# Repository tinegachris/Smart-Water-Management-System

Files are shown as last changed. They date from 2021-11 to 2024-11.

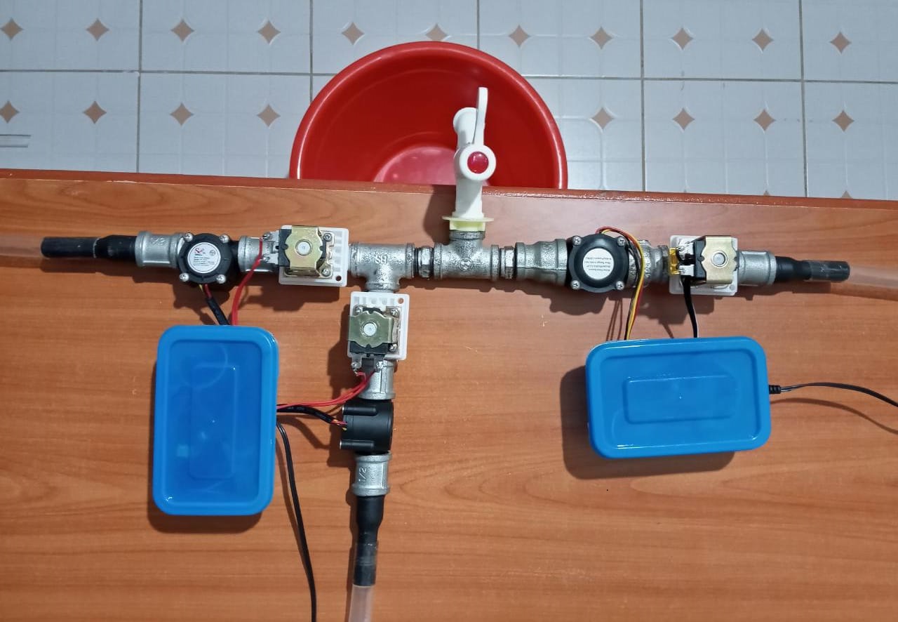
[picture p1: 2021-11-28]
system pic.jpeg

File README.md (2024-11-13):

# Smart-Water-Management-System

>Final Project 2021











system pic

## Abstract

The Smart Water Management System project aggregates three meters to enable remote and automatic real-time measurement of water consumption. Based on actionable decisions such as water leakage and consumption metrics, water supply through the pipes is controlled using solenoid valves. The consumer and the supplier can monitor, visualize consumption metrics and control the system through the designed android interface.

## Acknowledgement

I acknowledge the efforts of my project partner Mr [Thoenes Kimani](https://www.linkedin.com/in/thoenes-kimani-607682186/) and my project supervisor Mr [Samson N. Njoroge](https://www.linkedin.com/in/samson-n-njoroge-23a77817/?originalSubdomain=ke), for ensuring this project was successful. Many thanks to all our friends and family for the encouragement and support throughout the period.

## System Overview

The system consists of four functional modules, namely: the physical device, the gateway through which the device communicates with the backend service, the backend that allows storage of data, analysis, data access and notifications and the interface that allows visualization and control.

>

## Concept Diagram

The Concept Diagram provides an overview of the system's architecture, illustrating the main components and their relationships. It helps in understanding the high-level design and the flow of data between different parts of the system.

The system consists of three meters: the supply meter, 1 and customer meters, 2 and 3 as shown below.

>

You can view and edit the detailed Concept Diagram using the provided `.vsdx` file using Microsoft Visio app:

- [Concept Diagram.vsdx](https://github.com/tinegachris/Smart-Water-Management-System/blob/e62496e4574b8286091f124c95a754fc847280cd/Concept%20Diagram.vsdx)

## System Flow Chart

The System Flow Chart illustrates the step-by-step flow of operations within the Smart Water Management System. It shows the sequence of actions and decision points, making it easier to understand the system's logic and workflow.

>

You can view and edit the detailed System Flow Chart using the provided `.vsdx` file using Microsoft Visio app:

- [System Flow Chart.vsdx](https://github.com/tinegachris/Smart-Water-Management-System/blob/e62496e4574b8286091f124c95a754fc847280cd/System%20flow%20chart.vsdx)

## System Components

1. **Three NodeMCU ESP8266** - [Component Overview](https://components101.com/development-boards/nodemcu-esp8266-pinout-features-and-datasheet)
2. **Three YF-S201 Hall Effect Water Flow Sensor** - [Component Overview](https://components101.com/sensors/yf-s201-water-flow-measurement-sensor)
3. **Three 2 Way, 2 Position, 12 VDC, 0.5 Inch, NC Solenoid Valve** - [Particular](https://www.twinschip.com/Solenoid_Valve_DC12V_0.5inch_Normally_Closed) ~~Not an affiliate link~~
4. **Three SRD-05VDC-SL-C Relay Module** - [Component Overview](https://elearn.ellak.gr/mod/book/view.php?id=4568&chapterid=2440)
5. **Three Power Supply Adapter 12V 2A**
6. **0.5 Inch Clear hose pipe - approx. 3 meters**
7. **One 0.5 Inch Plastic tap**
8. **Appropriate pipe fittings**

## Schematic Diagram

The schematic diagram of the system was designed using Autodesk's Eagle EDA software illustrating how the various components are interconnected.

Custom libraries for the solenoid valve and the water flow sensor were created.

>sch

## PCB Design

Design of the board from the schematic diagram was done as shown below.

>brd

## Firmware Walkthrough

- **Libraries**

The ESP8266WiFi, ESP8266WebServer, ESP8266mDNS and the ThingSpeak libraries were included.

```
#include <ESP8266WiFi.h> // ESP8266WiFi library
#include<ESP8266WebServer.h> // WebServer library
#include <ESP8266mDNS.h> // mDNS library
#include<ThingSpeak.h> // ThingSpeak library
```

- **Variables and Constants**

The variables and constants were defined as follows.

```
const int measuringInterval = 0.1 * 1000; // measure flow every 1 second
const int postingInterval = 15 * 1000; // post data every 15 seconds

long currentMillis = 0, previousMillis = 0;

float calibrationFactor_1 = 0.1;
volatile byte pulseCount_1;
byte pulse1Sec_1 = 0;
float flowRate_1;
unsigned long flowMilliLitres_1, totalMilliLitres_1;
float flowLitres_1, totalLitres_1;

// Control solenoid valve
const int controlChannelID = XXXXXXX; //ThingSpeak channel used for control
unsigned int valve1 = 4;
```

- **Wi-Fi Settings**

The SSID and password are set to allow the NodeMCU to connect to a network

```
const char* ssid = "mySSID"; // wireless network name (SSID)
const char* password = "myPassword"; // Wi-Fi network password
```

- **ThingSpeak Settings**

ThingSpeak credentials and API key are set to allow sending data to specific channel.

```
// ThingSpeak Settings
const int channelID = YYYYYYY;
String writeAPIKey = "XXXXXXXXXXXXXXXX";
const char* server = "api.thingspeak.com";
```

- **Serial Communication**

The baud rate for serial communication  set was to 115200.

```
  void setup() {
  Serial.begin(115200); // Start the Serial communication
  delay(100);
```

- **Define pins and initialize variables**

```
  pulseCount_1 = 0;
  flowRate_1 = 0.0;
  flowMilliLitres_1 = 0;
  totalMilliLitres_1 = 0;
  
  pinMode(flowSensor_1, INPUT_PULLUP);  
  pinMode(relayValve_1, OUTPUT);
  digitalWrite(relayValve_1, 0);
```

- **Connect to Wi-Fi network**

The NodeMCU waits until it is connected to a network then sends the IP address, Netmask and Gateway to the serial monitor.

```
WiFi.begin(ssid, password);             // Connect to the WiFi network
  Serial.print("Connecting to ");
  Serial.print(ssid); Serial.println("...");

  while (WiFi.status() != WL_CONNECTED) { // Wait for the Wi-Fi to connect
    delay(500);
  }
  
  Serial.println("WiFi connected!"); 
  // Send the IP address of the ESP8266 to serial monitor 
  Serial.print("IP address:\t");
  Serial.println(WiFi.localIP()); 
  // Send the Netmask of the ESP8266        
  Serial.print("Netmask:\t");
  Serial.println(WiFi.subnetMask());  
  // Send the Gateway of the ESP8266
  Serial.print("Gateway:\t");
  Serial.println(WiFi.gatewayIP());
```

- **Measure Wi-Fi Strength**

The Wi-Fi strength is measured and sent to the serial monitor.

```
// Measure Signal Strength (RSSI) of Wi-Fi connection
long rssi = WiFi.RSSI();
String strgth = String(rssi);
Serial.println("signal strength: " + strgth + "dB\n");
```

- **HTTP server**

The HTTP server that listens for HTTP request on port 80. The mDNS responder is also started to resolve IP address to a local domain name.

```
  // Create a webserver object that listens for HTTP request on port 80
  ESP8266WebServer server(80);

  // Start the mDNS responder for esp8266.local
  if (MDNS.begin("esp8266")) {              
  Serial.println("mDNS responder started");
  } else {
    Serial.println("Error setting up MDNS responder!");
  }

  server.begin(); // Actually start the server
  Serial.println("HTTP server started");
  
  //create interrupt and call a function when change is detected
  attachInterrupt(digitalPinToInterrupt(flowSensor_1), pulseCounter_1, FALLING);

  ThingSpeak.begin(client);
```

- **FLow Sensor Interrrupt**

An interrupt and a call function is created to detect water flow when the falling edge of the pulse is received.

```
//create interrupt and call a function when change is detected
  attachInterrupt(digitalPinToInterrupt(flowSensor_1), pulseCounter_1, FALLING);
```

The pulse count is incremented for every pulse that is detected.

```
void IRAM_ATTR pulseCounter_1(){
  pulseCount_1++;
}
```

- **Flowrate and Volume Calculation**

The flowrate and volume through the meter is measured and calculated after every measuring interval. The total volume is the cumulative volume in the entire measuring time.

```
currentMillis = millis();
  // calculate after every measuring interval
  if (currentMillis - previousMillis > measuringInterval) {
    
    pulse1Sec_1 = pulseCount_1;
    pulseCount_1 = 0;

     //calculate flow rate in litres per min
    flowRate_1 = ((1000.0 / (millis() - previousMillis)) * pulse1Sec_1) / calibrationFactor_1;
    previousMillis = millis();

    //flowrate in millilitres per second
    flowMilliLitres_1 = (flowRate_1 / 60) * 1000;

    //flowrate in litres per second
    flowLitres_1 = (flowRate_1 / 60);

    //add volume flowed in this second to cumulative totals
    totalMilliLitres_1 += flowMilliLitres_1;
    totalLitres_1 += flowLitres_1;

    // Print the flow rate 1 for this second in litres / minute
    Serial.print("Flow rate 1: ");
    Serial.print(flowMilliLitres_1);
    Serial.print(" mL/s\t");
    
    // Print the cumulative total of litres flowed through meter 1 since starting
    Serial.print("Volume through meter 1: ");
    Serial.print(totalMilliLitres_1);
    Serial.print(" mL\n");
//    Serial.println("Volume through meter 1: "); //Uncomment for volume in litres
//    Serial.print(totalLitres_1);
//    Serial.println(" L\n");
```

- **API request body**

The body of API request with consumption data are constructed waiting to be posted to ThingSpeak on specific fields.

```
      // Construct API request body
      String body = "field1=";
      body += String(float(flowRate_1));
      body += "&field2=";
      body += String(totalMilliLitres_1);
      body += "&field3=";
      body += strgth;
      body += "\r\n\r\n";
```

- **Post to ThingSpeak**

The API requests bodies are written to the corresponding fields on ThingSpeak on the specified channel. Feedback on if the data was sent successfully is sent to the serial monitor.

```
      client.print("POST /update HTTP/1.1\n");
      client.print("Host: api.thingspeak.com\n");
      client.print("Connection: close\n");
      client.print("X-THINGSPEAKAPIKEY: " + writeAPIKey + "\n");
      client.print("Content-Type: application/x-www-form-urlencoded\n");
      client.print("Content-Length: ");
      client.print(body.length());
      client.print("\n\n");
      client.print(body);
      client.print("\n\n");
      Serial.println("data sent\n");
```

- **Solenoid Valve Status**

The status of solenoid valve i.e. if it is open or closed is checked from the control feed and status sent to the serial monitor.

```
      //get the last data of the fields
      int valve_1 = ThingSpeak.readFloatField(controlChannelID, valve1);
    
      if(valve_1 == 1){
        digitalWrite(relayValve_1, 1); // Open solenoid valve
        Serial.println("Solenoid valve is Closed!\n");
        }
      else if(valve_1 == 0){
        digitalWrite(relayValve_1, 0); //Close solenoid valve
        Serial.println("Solenoid valve is Open!\n");
        }
```

- **Wait and Post Again**

```
    client.stop();
    
    Serial.print("Waiting ");
    Serial.print(postingInterval/1000);
    Serial.print(" seconds to post again...\n");
    
    // wait and then post again
    delay(postingInterval);
```

## **ThingSpeak Apps**

- ### MATLAB Analysis

The MATLAB Analysis app was used to perform loss analysis as shown below.

>

- ### ThingTweet

The ThingTweet app is utilized to send alert consumers via a tweet that the supply meter valve is closed due to any predetermined circumstance is encountered. The tweet is configured as below.

>

- ### TimeControl

TimeControl app feature was used in loss analysis calculation where losses due to leakages was calculated every 5 minutes as shown in the configuration below.

>

- ### React

React app feature was also used in the project in several instances such as sending email, SMS and VoIP calls when a certain condition is encountered.

>

## App Installation and Usage Instructions

### Installing the Smart Water App

#### For Developers (Using .aia File)

1. **Download the .aia File:**
   - Download the [Smart_Water_App.aia](https://github.com/tinegachris/Smart-Water-Management-System/blob/main/Smart_Water_App.aia) file from the repository.

2. **Open MIT App Inventor:**
   - Go to [MIT App Inventor](https://appinventor.mit.edu/).

3. **Import the .aia File:**
   - Click on "Projects" in the top menu.
   - Select "Import project (.aia) from my computer".
   - Choose the downloaded .aia file and click "OK".

4. **Build the App:**
   - After importing, you can modify the app as needed.
   - To build the app, click on "Build" in the top menu and select "App (provide QR code for .apk)" or "App (save .apk to my computer)".

#### For Users (Using .apk File)

1. **Download the .apk File:**
   - Download the [Smart_Water_App.apk](https://github.com/tinegachris/Smart-Water-Management-System/blob/main/Smart_Water_App.apk) file from the repository.

2. **Enable Unknown Sources:**
   - On your Android device, go to "Settings".
   - Navigate to "Security" or "Applications" (depending on your device).
   - Enable "Unknown sources" to allow installation of apps from sources other than the Google Play Store.

3. **Install the App:**
   - Open the downloaded .apk file on your Android device.
   - Follow the on-screen instructions to install the app.

### Using the Smart Water App

1. **Open the App:**
   - Locate the Smart Water App icon on your device and open it.

2. **Login:**
   - Enter your credentials to log in to the app.

3. **Monitor and Control:**
   - Use the app interface to monitor water consumption metrics.
   - Control the water supply through the solenoid valves remotely.

4. **Alerts and Notifications:**
   - Receive alerts and notifications for water leakage and other actionable events.

## **Interface**

The android app used as interface to visualize consumption data and control water supply remotely was designed using [MIT App Inventor](https://appinventor.mit.edu/).

The [.aia source code](https://github.com/tinegachris/Smart-Water-Management-System/blob/main/Smart_Water_App.aia) file is attached.

Download and install the [android app](https://github.com/tinegachris/Smart-Water-Management-System/blob/main/Smart_Water_App.app)

> login                   

## Results

The system utilized IoT solutions to enable remote and automatic and real-time measurement of water consumption data which is transmitted to a remote server for manipulation and analysis.

>

The data was then displayed on an interface where consumption metrics, over a period, was be viewed.

>                         

The system developed aggregated multiple meters and performed loss analysis hence detecting water leakage. SMS, call, email and [tweet](https://twitter.com/smart_water_app/status/1463631460607344641?t=qJkpamW6DDiH7IFD41dn9Q&s=19) alerts allowed appropriate actions to be taken.

> tweet               

Users could control water supply remotely from the interface based on actionable decisions.

> closed
> opened
> 

## Conclusion

The Smart Water Management System solution would be revolutionary for home and industrial systems by enabling remote and automatic measurement of consumption data, convenient monitoring and control of water systems and reducing water leakage - reducing non-revenue water hence saving on cost.

##

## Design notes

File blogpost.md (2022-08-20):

---
title: Smart Water Management System
domain: blog.chrispinetinega.com 
tags: Smart water system, Chrispine Tinega, IoT
subtitle: Final Project
/* The pathname of your article url 
* Ex. In https://engineering.hashnode.com/how-we-autodetect-spam-using-googles-vertex-ai 
"how-we-autodetect-spam-using-googles-vertex-ai" is the slug */ 
slug: smart-water-system
/* You need to upload your image to https://hashnode.com/uploader 
and use the uploaded image URL as COVER_IMAGE_URL */ 
cover: https://cdn.hashnode.com/res/hashnode/image/upload/v1660997561622/8FiyUe9cX.jpeg?auto=compress
/* When you have a team publication and a publication member has created an article */ 
/* Please note that this param is only supported while creating an article and not updating */ 
publishAs: Chrispine Tinega
/* When your article is republished and you want to use 
 the origin url as canonical url */ 
canonical: CANONICAL_URL_OF_ARTICLE 
/* Only if you don't want this article to be published yet */ 

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

>

## System Diagram
The system consists of three meters: the supply meter, 1 and customer meters, 2 and 3 as shown below.

>

## Flow Chart
The system’s flow chart diagram is as shown in the figure below.

>

## System Components

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

## Schematic Diagram

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

Custom libraries for the solenoid valve and the water flow sensor were created.

>sch

## PCB Design

Design of the board from the schematic diagram was done as shown below. 

>brd

## Firmware Walkthrough

- **Libraries**

The ESP8266WiFi, ESP8266WebServer, ESP8266mDNS and the ThingSpeak libraries were included.

```
#include <ESP8266WiFi.h> // ESP8266WiFi library
#include<ESP8266WebServer.h> // WebServer library
#include <ESP8266mDNS.h> // mDNS library
#include<ThingSpeak.h> // ThingSpeak library
```
- **Variables and Constants**

The variables and constants were defined as follows.
```
const int measuringInterval = 0.1 * 1000; // measure flow every 1 second
const int postingInterval = 15 * 1000; // post data every 15 seconds

long currentMillis = 0, previousMillis = 0;

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

// Control solenoid valve
const int controlChannelID = XXXXXXX; //ThingSpeak channel used for control
unsigned int valve1 = 4;
```

- **Wi-Fi Settings**

The SSID and password are set to allow the NodeMCU to connect to a network
```
const char* ssid = "mySSID"; // wireless network name (SSID)
const char* password = "myPassword"; // Wi-Fi network password
```

- **ThingSpeak Settings**

ThingSpeak credentials and API key are set to allow sending data to specific channel.
```
// ThingSpeak Settings
const int channelID = YYYYYYY;
String writeAPIKey = "XXXXXXXXXXXXXXXX";
const char* server = "api.thingspeak.com";
```

- **Serial Communication**

The baud rate for serial communication  set was to 115200.
```
  void setup() {
  Serial.begin(115200); // Start the Serial communication
  delay(100);
```

- **Define pins and initialize variables**

```
  pulseCount_1 = 0;
  flowRate_1 = 0.0;
  flowMilliLitres_1 = 0;
  totalMilliLitres_1 = 0;
  
  pinMode(flowSensor_1, INPUT_PULLUP);  
  pinMode(relayValve_1, OUTPUT);
  digitalWrite(relayValve_1, 0);
```

- **Connect to Wi-Fi network**

The NodeMCU waits until it is connected to a network then sends the IP address, Netmask and Gateway to the serial monitor.
```
WiFi.begin(ssid, password);             // Connect to the WiFi network
  Serial.print("Connecting to ");
  Serial.print(ssid); Serial.println("...");

  while (WiFi.status() != WL_CONNECTED) { // Wait for the Wi-Fi to connect
    delay(500);
  }
  
  Serial.println("WiFi connected!"); 
  // Send the IP address of the ESP8266 to serial monitor 
  Serial.print("IP address:\t");
  Serial.println(WiFi.localIP()); 
  // Send the Netmask of the ESP8266        
  Serial.print("Netmask:\t");
  Serial.println(WiFi.subnetMask());  
  // Send the Gateway of the ESP8266
  Serial.print("Gateway:\t");
  Serial.println(WiFi.gatewayIP());
```

- **Measure Wi-Fi Strength**

The Wi-Fi strength is measured and sent to the serial monitor.
```
// Measure Signal Strength (RSSI) of Wi-Fi connection
long rssi = WiFi.RSSI();
String strgth = String(rssi);
Serial.println("signal strength: " + strgth + "dB\n");
```

- **HTTP server**

The HTTP server that listens for HTTP request on port 80. The mDNS responder is also started to resolve IP address to a local domain name.
```
  // Create a webserver object that listens for HTTP request on port 80
  ESP8266WebServer server(80);

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

  ThingSpeak.begin(client);
```

- **FLow Sensor Interrrupt**

An interrupt and a call function is created to detect water flow when the falling edge of the pulse is received.
```
//create interrupt and call a function when change is detected
  attachInterrupt(digitalPinToInterrupt(flowSensor_1), pulseCounter_1, FALLING);
```
The pulse count is incremented for every pulse that is detected.
```
void IRAM_ATTR pulseCounter_1(){
  pulseCount_1++;
}
```

- **Flowrate and Volume Calculation**

The flowrate and volume through the meter is measured and calculated after every measuring interval. The total volume is the cumulative volume in the entire measuring time.
```
currentMillis = millis();
  // calculate after every measuring interval
  if (currentMillis - previousMillis > measuringInterval) {
    
    pulse1Sec_1 = pulseCount_1;
    pulseCount_1 = 0;

     //calculate flow rate in litres per min
    flowRate_1 = ((1000.0 / (millis() - previousMillis)) * pulse1Sec_1) / calibrationFactor_1;
    previousMillis = millis();

    //flowrate in millilitres per second
    flowMilliLitres_1 = (flowRate_1 / 60) * 1000;

    //flowrate in litres per second
    flowLitres_1 = (flowRate_1 / 60);

    //add volume flowed in this second to cumulative totals
    totalMilliLitres_1 += flowMilliLitres_1;
    totalLitres_1 += flowLitres_1;

    // Print the flow rate 1 for this second in litres / minute
    Serial.print("Flow rate 1: ");
    Serial.print(flowMilliLitres_1);
    Serial.print(" mL/s\t");
    
    // Print the cumulative total of litres flowed through meter 1 since starting
    Serial.print("Volume through meter 1: ");
    Serial.print(totalMilliLitres_1);
    Serial.print(" mL\n");
//    Serial.println("Volume through meter 1: "); //Uncomment for volume in litres
//    Serial.print(totalLitres_1);
//    Serial.println(" L\n");
```

- **API request body**

The body of API request with consumption data are constructed waiting to be posted to ThingSpeak on specific fields.
```
      // Construct API request body
      String body = "field1=";
      body += String(float(flowRate_1));
      body += "&field2=";
      body += String(totalMilliLitres_1);
      body += "&field3=";
      body += strgth;
      body += "\r\n\r\n";
```

- **Post to ThingSpeak**

The API requests bodies are written to the corresponding fields on ThingSpeak on the specified channel. Feedback on if the data was sent successfully is sent to the serial monitor.
```
      client.print("POST /update HTTP/1.1\n");
      client.print("Host: api.thingspeak.com\n");
      client.print("Connection: close\n");
      client.print("X-THINGSPEAKAPIKEY: " + writeAPIKey + "\n");
      client.print("Content-Type: application/x-www-form-urlencoded\n");
      client.print("Content-Length: ");
      client.print(body.length());
      client.print("\n\n");
      client.print(body);
      client.print("\n\n");
      Serial.println("data sent\n");
```

- **Solenoid Valve Status**

The status of solenoid valve i.e. if it is open or closed is checked from the control feed and status sent to the serial monitor.
```
      //get the last data of the fields
      int valve_1 = ThingSpeak.readFloatField(controlChannelID, valve1);
    
      if(valve_1 == 1){
        digitalWrite(relayValve_1, 1); // Open solenoid valve
        Serial.println("Solenoid valve is Closed!\n");
        }
      else if(valve_1 == 0){
        digitalWrite(relayValve_1, 0); //Close solenoid valve
        Serial.println("Solenoid valve is Open!\n");
        }
```

- **Wait and Post Again**

```
    client.stop();
    
    Serial.print("Waiting ");
    Serial.print(postingInterval/1000);
    Serial.print(" seconds to post again...\n");
    
    // wait and then post again
    delay(postingInterval);
```

## **ThingSpeak Apps**

- ### MATLAB Analysis 

The MATLAB Analysis app was used to perform loss analysis as shown below.

>

- ### ThingTweet

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

>

- ### TimeControl

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

>

- ### React

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

>

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

## Results

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

>

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

Users could control water supply remotely from the interface based on actionable decisions.

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

## Conclusion

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

##

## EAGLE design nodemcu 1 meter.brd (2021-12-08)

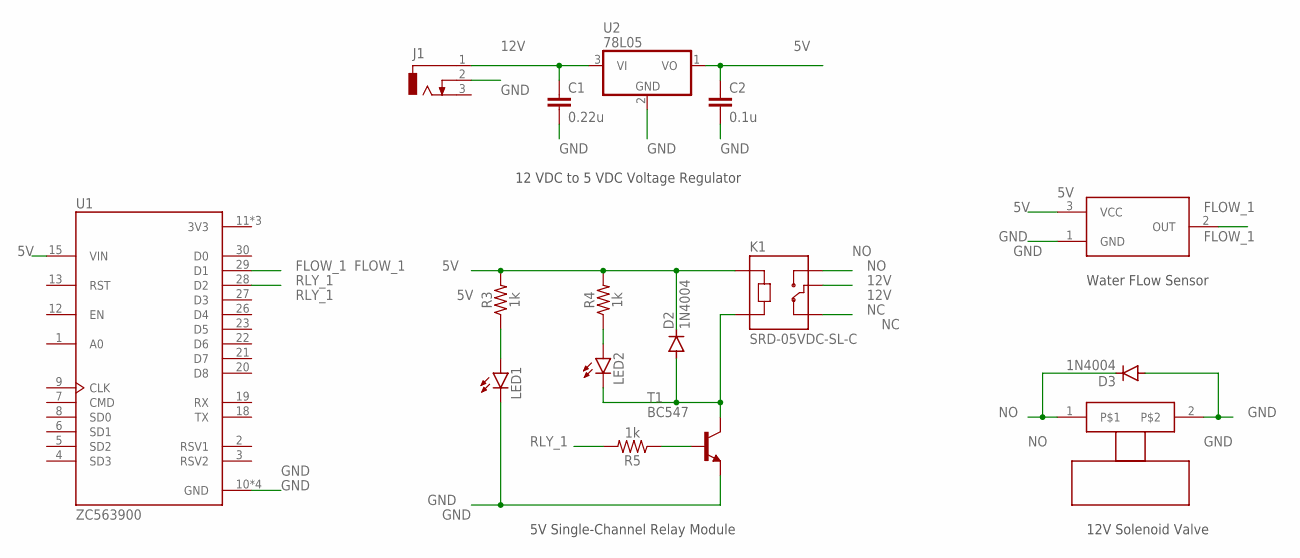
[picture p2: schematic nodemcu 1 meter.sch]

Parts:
C1: 0.22u; C025-025X050
C2: 0.1u; C025-025X050
D2, D3: 1N4004; DO41-10
FLOWSENSOR1: FLOWSENSOR
J1: DCJ0303
K1: SRD-05VDC-SL-C; RELAY_SRD-05VDC-SL-C
LED1, LED2: LED3MM
R3, R4, R5: 1k; AXIAL-0.3
T1: BC547; TO92
U1: ZC563900; MODULE_ZC563900
U2: 78L05; TO92
VALVE1: SOLENOID-VALVESOLENOID-CONNECTOR; 332-02

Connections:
3V3: U1.11 (3V3), U1.16 (3V3), U1.25 (3V3)
5V: C2.2, D2.C, FLOWSENSOR1.3 (VCC), K1.A1, R3.P$2 (2), R4.P$2 (2), U1.15 (VIN), U2.1 (VO)
12V: C1.2, J1.1, K1.COM, U2.3 (VI)
FLOW_1: FLOWSENSOR1.2 (OUT), U1.29 (D1)
GND: C1.1, C2.1, D3.A, FLOWSENSOR1.1 (GND), J1.2, LED1.K (C), T1.1 (E), U1.10 (GND), U1.14 (GND), U1.17 (GND), U1.24 (GND), U2.2 (GND), VALVE1.2
unnamed: R5.P$1 (1), T1.2 (B)
unnamed: D2.A, K1.A2, LED2.K (C), T1.3 (C)
unnamed: LED2.A, R4.P$1 (1)
unnamed: LED1.A, R3.P$1 (1)
NC: K1.NC
NO: D3.C, K1.NO, VALVE1.1
RLY_1: R5.P$2 (2), U1.28 (D2)

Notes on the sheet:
5V Single-Channel Relay Module
Water FLow Sensor
12V Solenoid Valve
12 VDC to 5 VDC Voltage Regulator

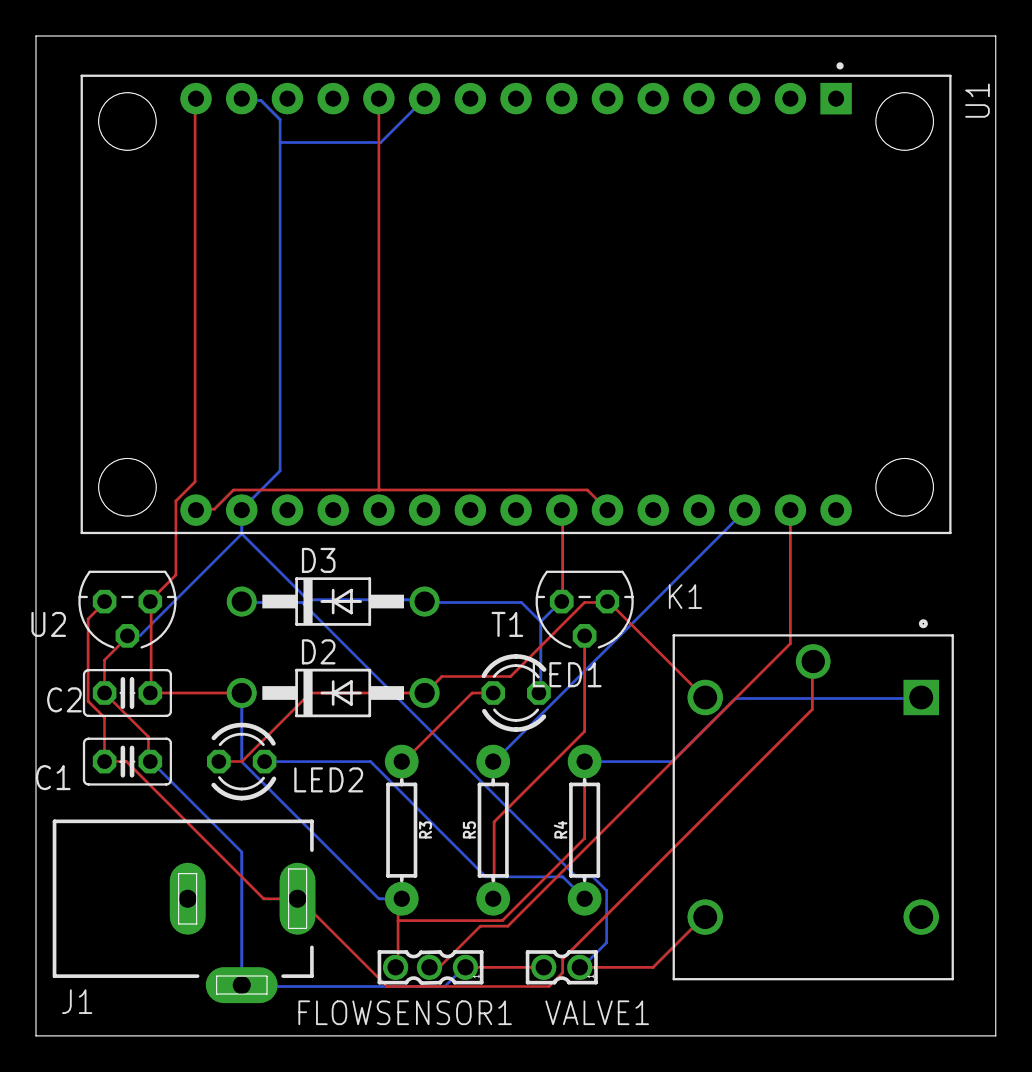
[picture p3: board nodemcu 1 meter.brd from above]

Board: 2 copper layers, 53.3 x 55.5 mm, 16 parts (0 on the bottom side), 11 nets.

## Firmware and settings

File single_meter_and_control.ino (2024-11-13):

/* *****SMART WATER MANAGEMENT SYSTEM*****

  This project aggregates 3 flow sensors, sends consumption data to ThingSpeak IoT platform for visualization,
  controls water flow based on actionable decisions and detects water leakage.

  Author(s): Chrispine Tinega
          Thoenes Kimani

  Last Edited: Monday November 22, 2021

  All Rights Reserved.
*/

#include <ESP8266WiFi.h> // ESP8266WiFi library
#include <ESP8266WebServer.h> // WebServer library
#include <ESP8266mDNS.h> // mDNS library
#include <ThingSpeak.h> // ThingSpeak library

// Pin Definitions
#define LED_BUILTIN 16 // GPIO 16 i.e. D0
#define FLOW_SENSOR_1 5 // flowsensor of meter 1 connected to D1 i.e. GPIO 5
#define RELAY_VALVE_1 4 // relay input signal pin connected to D2 i.e GPIO 4

// Timing Constants
const int MEASURING_INTERVAL = 100; // measure flow every 0.1 second
const int POSTING_INTERVAL = 15000; // post data every 15 seconds

// Calibration Factor
const float CALIBRATION_FACTOR_1 = 0.1;

// Wi-Fi Settings
const char* SSID = "whisperygeek"; // wireless network name (SSID)
const char* PASSWORD = "qwerty9516"; // Wi-Fi network password

// ThingSpeak Settings
const int CHANNEL_ID = 1583388;
const String WRITE_API_KEY = "Y7A8COY3CXGDW83A";
const char* SERVER = "api.thingspeak.com";

// Control solenoid valve
const int CONTROL_CHANNEL_ID = 1583388;
const unsigned int VALVE_1 = 4;

// Global Variables
long currentMillis = 0, previousMillis = 0;
volatile byte pulseCount_1;
byte pulse1Sec_1 = 0;
float flowRate_1;
unsigned long flowMilliLitres_1, totalMilliLitres_1;
float flowLitres_1, totalLitres_1;

WiFiClient client; // create a Wi-Fi client to connect to ThingSpeak

void IRAM_ATTR pulseCounter_1() {
  pulseCount_1++;
}

void connectToWiFi() {
  WiFi.begin(SSID, PASSWORD); // Connect to the WiFi network
  Serial.print("Connecting to ");
  Serial.print(SSID); Serial.println("...");

  while (WiFi.status() != WL_CONNECTED) { // Wait for the Wi-Fi to connect
   delay(500);
  }

  Serial.println("WiFi connected!");
  Serial.print("IP address:\t");
  Serial.println(WiFi.localIP());
  Serial.print("Netmask:\t");
  Serial.println(WiFi.subnetMask());
  Serial.print("Gateway:\t");
  Serial.println(WiFi.gatewayIP());
}

void setupMDNS() {
  if (MDNS.begin("esp8266")) {
   Serial.println("mDNS responder started");
  } else {
   Serial.println("Error setting up MDNS responder!");
  }
}

void setup() {
  Serial.begin(115200); // Start the Serial communication
  delay(100);

  pulseCount_1 = 0;
  flowRate_1 = 0.0;
  flowMilliLitres_1 = 0;
  totalMilliLitres_1 = 0;

  pinMode(FLOW_SENSOR_1, INPUT_PULLUP);
  pinMode(RELAY_VALVE_1, OUTPUT);
  digitalWrite(RELAY_VALVE_1, LOW);

  Serial.println('\n');

  connectToWiFi();
  setupMDNS();

  // Create a webserver object that listens for HTTP request on port 80
  ESP8266WebServer server(80);
  server.begin(); // Actually start the server
  Serial.println("HTTP server started");

  // Create interrupt and call a function when change is detected
  attachInterrupt(digitalPinToInterrupt(FLOW_SENSOR_1), pulseCounter_1, FALLING);

  ThingSpeak.begin(client);
}

void sendDataToThingSpeak() {
  if (client.connect(SERVER, 80)) {
   // Measure Signal Strength (RSSI) of Wi-Fi connection
   long rssi = WiFi.RSSI();
   String strgth = String(rssi);
   Serial.println("Signal strength: " + strgth + "dB\n");

   // Construct API request body
   String body = "field1=" + String(float(flowRate_1)) +
            "&field2=" + String(totalMilliLitres_1) +
            "&field3=" + strgth + "\r\n\r\n";

   client.print("POST /update HTTP/1.1\n");
   client.print("Host: " + String(SERVER) + "\n");
   client.print("Connection: close\n");
   client.print("X-THINGSPEAKAPIKEY: " + WRITE_API_KEY + "\n");
   client.print("Content-Type: application/x-www-form-urlencoded\n");
   client.print("Content-Length: " + String(body.length()) + "\n\n");
   client.print(body);
   client.print("\n\n");
   Serial.println("Data sent\n");

   // Get the last data of the fields
   int valve_1 = ThingSpeak.readFloatField(CONTROL_CHANNEL_ID, VALVE_1);

   if (valve_1 == 1) {
    digitalWrite(RELAY_VALVE_1, HIGH); // Open solenoid valve
    Serial.println("Solenoid valve is Closed!\n");
   } else if (valve_1 == 0) {
    digitalWrite(RELAY_VALVE_1, LOW); // Close solenoid valve
    Serial.println("Solenoid valve is Open!\n");
   }

   client.stop();
  }
}

void loop() {
  currentMillis = millis();
  // Calculate after every measuring interval
  if (currentMillis - previousMillis > MEASURING_INTERVAL) {
   pulse1Sec_1 = pulseCount_1;
   pulseCount_1 = 0;

   // Calculate flow rate in litres per min
   flowRate_1 = ((1000.0 / (millis() - previousMillis)) * pulse1Sec_1) / CALIBRATION_FACTOR_1;
   previousMillis = millis();

   // Flow rate in millilitres per second
   flowMilliLitres_1 = (flowRate_1 / 60) * 1000;

   // Flow rate in litres per second
   flowLitres_1 = (flowRate_1 / 60);

   // Add volume flowed in this second to cumulative totals
   totalMilliLitres_1 += flowMilliLitres_1;
   totalLitres_1 += flowLitres_1;

   // Print the flow rate 1 for this second in litres / minute
   Serial.print("Flow rate 1: ");
   Serial.print(flowMilliLitres_1);
   Serial.print(" mL/s\t");

   // Print the cumulative total of litres flowed through meter 1 since starting
   Serial.print("Volume through meter 1: ");
   Serial.print(totalMilliLitres_1);
   Serial.print(" mL\n");

   sendDataToThingSpeak();

   Serial.print("Waiting ");
   Serial.print(POSTING_INTERVAL / 1000);
   Serial.print(" seconds to post again...\n");

   // Wait and then post again
   delay(POSTING_INTERVAL);
  }
}

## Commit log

2021-11-28 concept diagram & system flow chart upload
2021-11-28 eagle schematic file upload
    [nodemcu 1 meter.sch]
2021-12-08 Board design and eagle sch upload
    [nodemcu 1 meter.brd, nodemcu 1 meter.sch]

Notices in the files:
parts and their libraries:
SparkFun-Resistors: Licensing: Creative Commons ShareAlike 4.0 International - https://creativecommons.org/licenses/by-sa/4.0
